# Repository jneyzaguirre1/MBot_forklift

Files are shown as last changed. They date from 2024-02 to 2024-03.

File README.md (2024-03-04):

# MBot_forklift
Welcome, this repository is about a Forklift Design for the Botlab competition at ROB550: Robotics Systems Laboratory, from the University of Michigan. I took this class in fall 2023, at my first semester of my MS in robotics. 

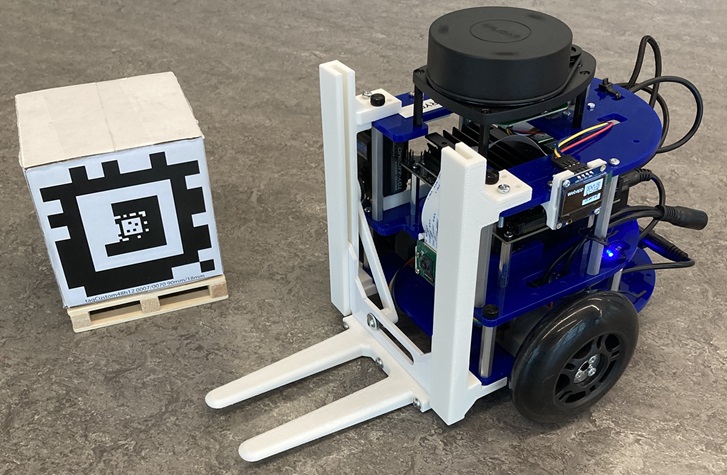
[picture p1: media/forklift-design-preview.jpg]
Forklift Design Preview


ROB550 is divided into two projects: Armlab, and Botlab. Students are divided in groups of three, and for the botlab, each of them gets an MBOT (Michigan's educational bot). For this part of the class we had to calibrate the motors, implement the velocity and position control for the robot, SLAM, path planning, and design a forklift for a new special task for this year's competition.

This repository presents:
- A video demonstration
- The design principles we had for the forklift.
- The design analysis.
- The design files.

## Video demonstration
[Forklift Video Demonstration]

## Design principles

The forklift design was guided by three main principles: 1) simplicity, 2) minimize interference with the MBot, and 3) inexpensive and easy to manufacture.

The lifting mechanism converts rotational motion into two linear components, which enabled fast response times and motion achieved via a single actuator. A single servo rotated a solid link, which traveled linearly in a slot attached to the forklift. As the servo rotated, the end of the link moved horizontally in the slot and moved the forklift vertically. The forklift was constrained to move vertically via two rails on either side of the lift. 

The design has 8 main components. We used a hobby servo enabling simple hardware integration and high-level control with an internal feedback control loop for precise motion. The hobby servo used was part of the available components in the class' laboratory. To minimize MBot interference, we designed the forklift as close to the MBot as possible. With the forklift, the turning radius changed from 125 mm to 175 mm, and neither the camera nor the Lidar were occluded at the main positions. The custom parts were manufactured by 3D printing with a FDM Creality Ender 3 V3 SE printer, and by laser cutting acrylic, where both tools are available in the robotics department. Some small components were purchased, including a few fasteners and a bearing that allowed low friction for the linear motion along the slot.

## Design analysis

We performed a simple static force-torque analysis to choose the correct servo motor. We start by analyzing the wrenches involved in the front panel that slides in the lateral rails of the forklift (Fig. [1](#diagram)), and we do the same for the rod that connects the hobby servo to the front panel (Fig. [2](#rod)). 

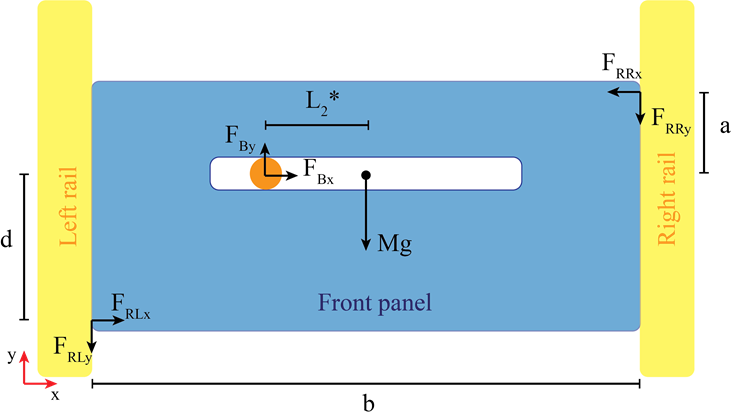
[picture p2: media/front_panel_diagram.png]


Assumptions:
- The center of mass of the front panel lies on the horizontal path were the bearing moves.
- Coulomb friction model.
- The contact force between the bearing and the front panel is normal to the surface: *F<sub>x<sub>B</sub></sub> = 0*.
- The contact points between the front panel and the lateral rails lie on opposite extreme points, and exists due to the torque produce by the connecting rod into the front panel.

Given that the sum of forces and torques are equal to zero, we can derive the following expressions:

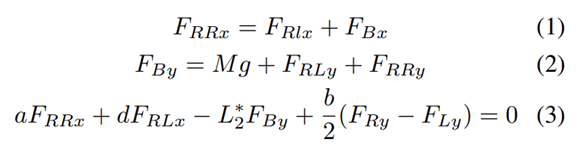
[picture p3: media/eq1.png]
Equations 1


As *F<sub>Bx</sub> = 0*, then *F<sub>RLx</sub> = F<sub>RRx</sub> = F<sub>Rx</sub>*. By coulomb friction model we know that *F<sub>RLy</sub> = μ F<sub>RLx</sub> = μ F<sub>Rx</sub>* and the same happens for *F<sub>RRy</sub> = μ F<sub>Rx</sub>*. Combining this information with the equations above we get the following expression:

Equations 2

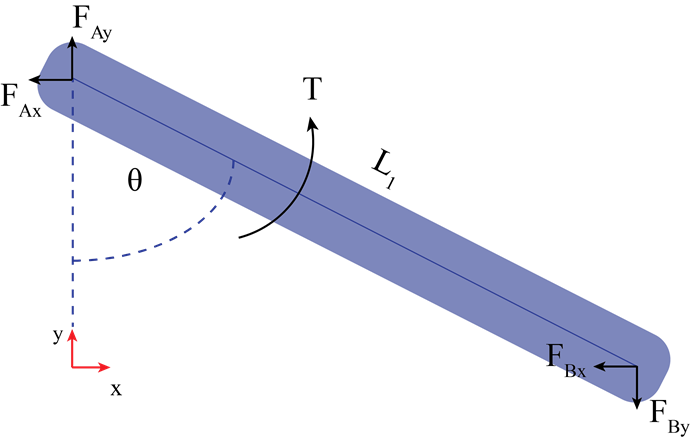
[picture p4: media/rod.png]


Following the same procedure for the rod connecting the servo motor and the front panel, we get the following equations:

Equations 3

What we are left to define is *L<sub>2</sub><sup>*</sub>*, which if we consider the distance in *x* between the motor shaft and the center of mass of the front panel as *c*, it can be expressed as *L<sub>2</sub><sup>*</sup> = c - L<sub>1</sub> sin(θ)*. In this design *c = 64.8* mm.

In order to give values to the different constants, we now define two more parameters: the vertical stroke *s* of the forklift and the total angular displacement *ω* for that stroke. The vertical stroke is given by the height of the pallets to be lifted, which is around 125 mm. We consider then *s* to be 135 mm and due to some geometrical restrictions of the design *ω = 110°*. We can then relate *L<sub>1</sub>* with these two parameters as follow:

Equations 4

Plotting the torque *Τ* vs *ω* for the following parameters, gives us an approximation of the required torque for the motor: *μ=0.7*, *M=0.1* Kg, *a=0.04* m, and *d = 0.01* m. The maximum is achieved at the extremes angles, and has a value of 0.091 Nm.

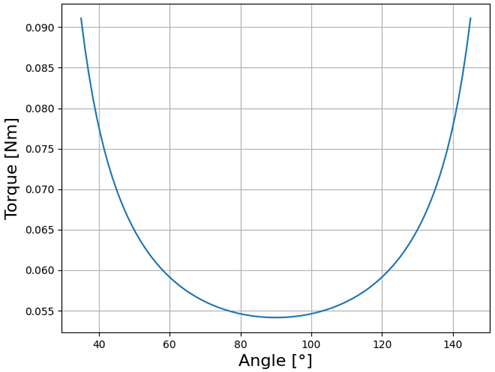
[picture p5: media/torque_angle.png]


## Design files
The design files can be found in the `design` folder. There you are going to find a fusion 360 file of the forklift assembly, and a bill of materials. In the `STLs` folder the STLs of the 3D printed parts are found, and a dxf for laser cut the front panel.

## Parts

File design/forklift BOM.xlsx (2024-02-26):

PARTS LIST
ITEM | QTY | PART NUMBER | DESCRIPTION | MATERIAL | LINK
1 | 1 | MBOT - FULL ASSEMBLY - MOD | MBOT - WITH MIDDLE PLATE MODIFICATION
2 |  | RAILS
2.1 | 1 | RAIL_LEFT | CUSTOM 3D PRINTED PART | ABS PLASTIC
2.2 | 1 | RAIL_RIGHT | CUSTOM 3D PRINTED PART | ABS PLASTIC
3 | 1 | PANEL_FRONT |  | ACRYLIC
4 | 1 | FORKS | CUSTOM 3D PRINTED PART | ABS PLASTIC
5 | 1 | BUSHING | CUSTOM 3D PRINTED PART | ABS PLASTIC
6 | 1 | BEARING 4MM ID |  | STEEL | https://www.amazon.com/uxcell-Bearing-Double-Shielded-Bearings/dp/B07FW1958S
7 | 1 | CONNECTING ROD | CUSTOM 3D PRINTED PART | ABS PLASTIC
8 | 1 | TGY4409MD | SERVO MOTOR | STEEL | http://www.jx-servo.com/en/Product/LOW/437.html
9 |  | MOTOR_SUPPORTS
9.1 | 1 | MOTOR_SUPPORT_UP | CUSTOM 3D PRINTED PART | ABS PLASTIC
9.2 | 1 | MOTOR_SUPPORT_DOWN | CUSTOM 3D PRINTED PART | ABS PLASTIC
10 | 4 | 92095A125 | M4 X 15MM BUTTON HEAD HEX DRIVE SCREW | STEEL | https://www.mcmaster.com/92095A125/
11 | 1 | 91100A130 | ZINC-PLATED STEEL OVERSIZED WASHER | STEEL | https://www.mcmaster.com/91100A130/
12 | 4 | 90631A112 | M4 NYLON-INSERT LOCKNUT | STEEL | https://www.mcmaster.com/90631A112/
13 | 4 | 91185A245 | THUMB SCREWS KNURLED 4-40 5/8" |  | https://www.mcmaster.com/91185A245/
14 | 8 | 94180A321 | M2.5 BRASS INSERT | BRASS | https://www.mcmaster.com/94180A321/
15 | 8 | 92005A069 | PAN HEAD PHILLIPS SCREW M2.5 X 8 | STEEL | https://www.mcmaster.com/92005A069/
16 | 4 | 93475A196 | M2.5 WASHER | STAINLESS STEEL | https://www.mcmaster.com/93475A196/
17 | 4 | 94997A130 | M2.2 SELF TAPPING SCREW | STEEL | https://www.mcmaster.com/94997A130/
18 | 4 | 90576A102 | M3 LOCKNUT | STEEL | https://www.mcmaster.com/90576A102/
19 | 4 | 92000A126 | M3 X 16 SCREW | STEEL | https://www.mcmaster.com/92000A126/

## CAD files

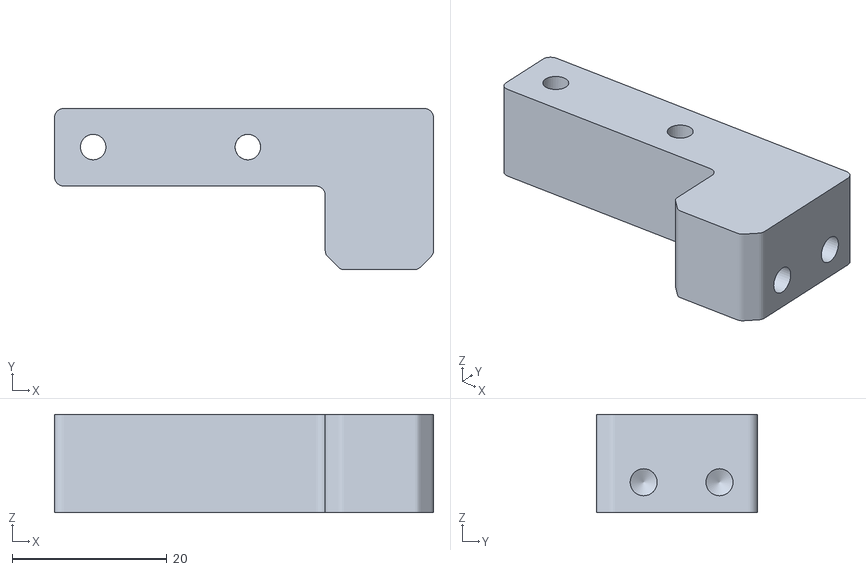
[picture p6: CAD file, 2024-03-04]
STLs/motor_support_up.stl
49.0 x 20.8 x 12.7

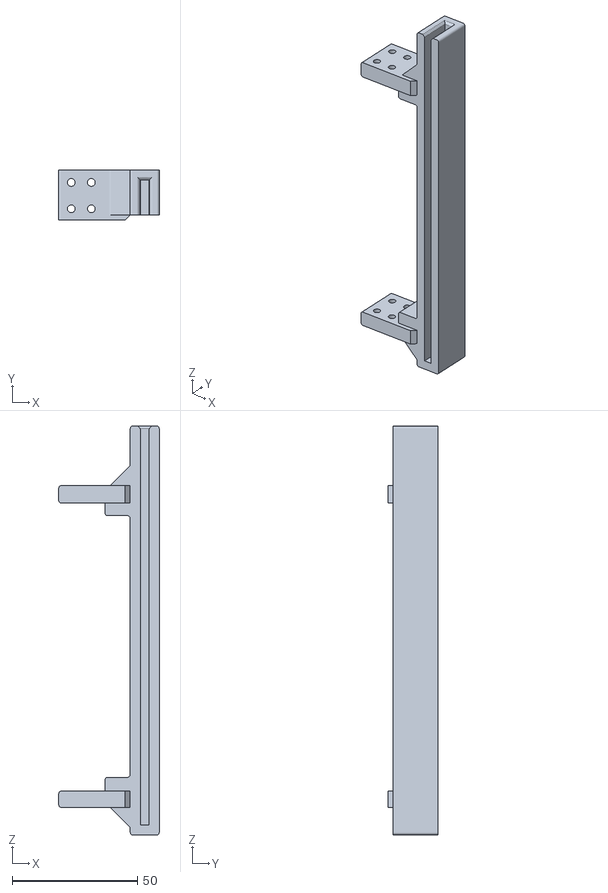
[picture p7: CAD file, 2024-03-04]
STLs/rails_right.stl
40.1 x 20.0 x 163.0

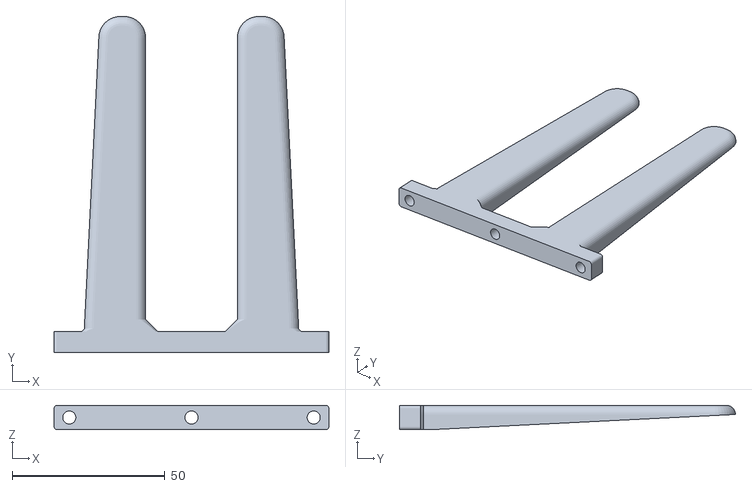
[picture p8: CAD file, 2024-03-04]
STLs/Forks.stl
90.0 x 110.0 x 8.00

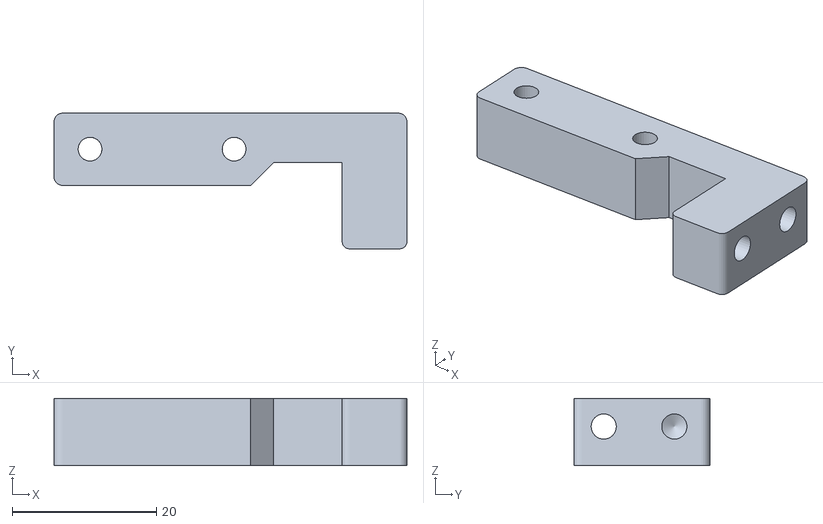
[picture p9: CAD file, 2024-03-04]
STLs/motor_support down.stl
49.0 x 18.8 x 9.35

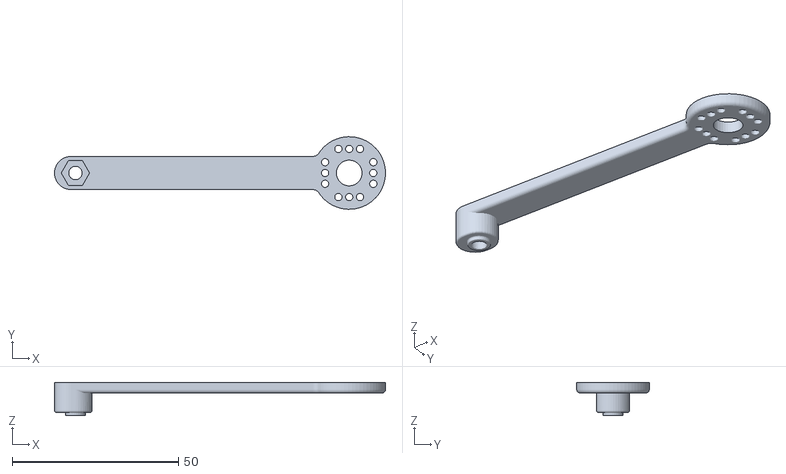
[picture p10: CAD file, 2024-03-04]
STLs/connecting_rod.stl
99.6 x 21.8 x 9.99

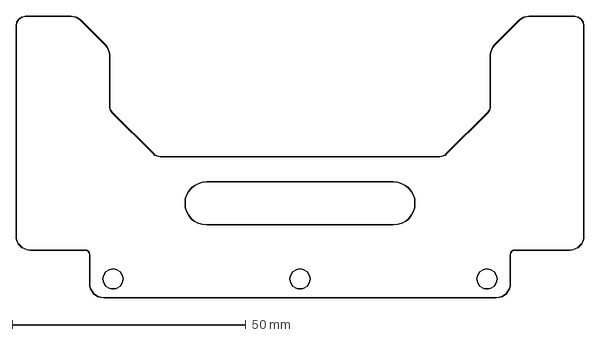
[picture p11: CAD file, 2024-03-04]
STLs/panel_front.dxf
121.5 x 60.2 mm

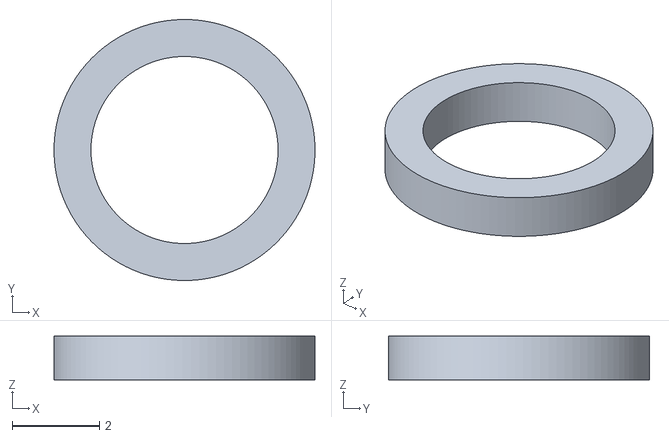
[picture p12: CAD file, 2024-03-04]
STLs/bushing.stl
6.00 x 6.00 x 1.00

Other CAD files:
STLs/rail_left.stl

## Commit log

2024-02-23 added media and fusion assembly
2024-02-26 added BOM
    [forklift BOM.xlsx]
2024-03-04 Added STLs
    [Forks.stl, bushing.stl, connecting_rod.stl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]
